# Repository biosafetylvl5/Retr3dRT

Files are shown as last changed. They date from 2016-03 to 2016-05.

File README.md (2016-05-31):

# Retr3dRT
RAMPS 1.4 self-test board designed for used in conjunction with Retr3d.

## Images
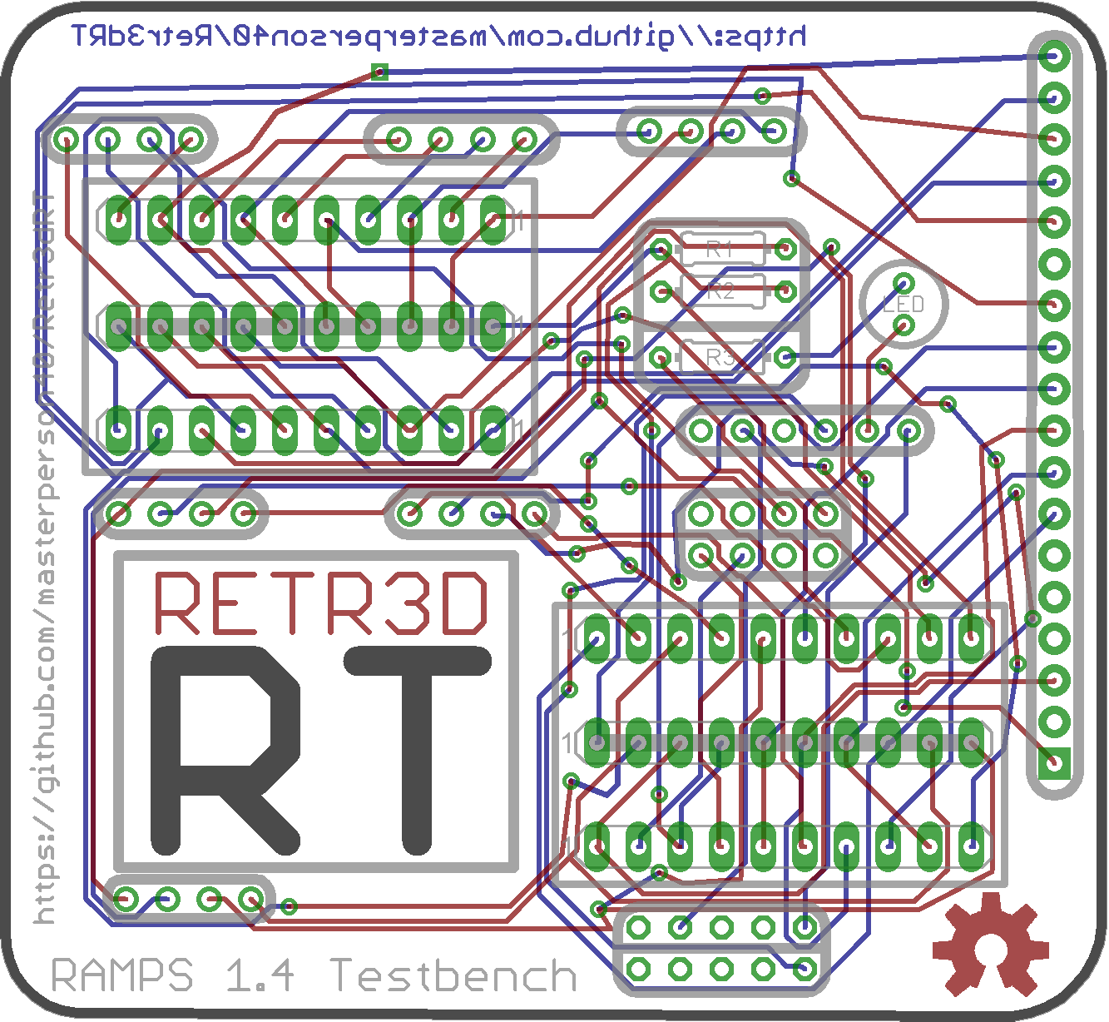
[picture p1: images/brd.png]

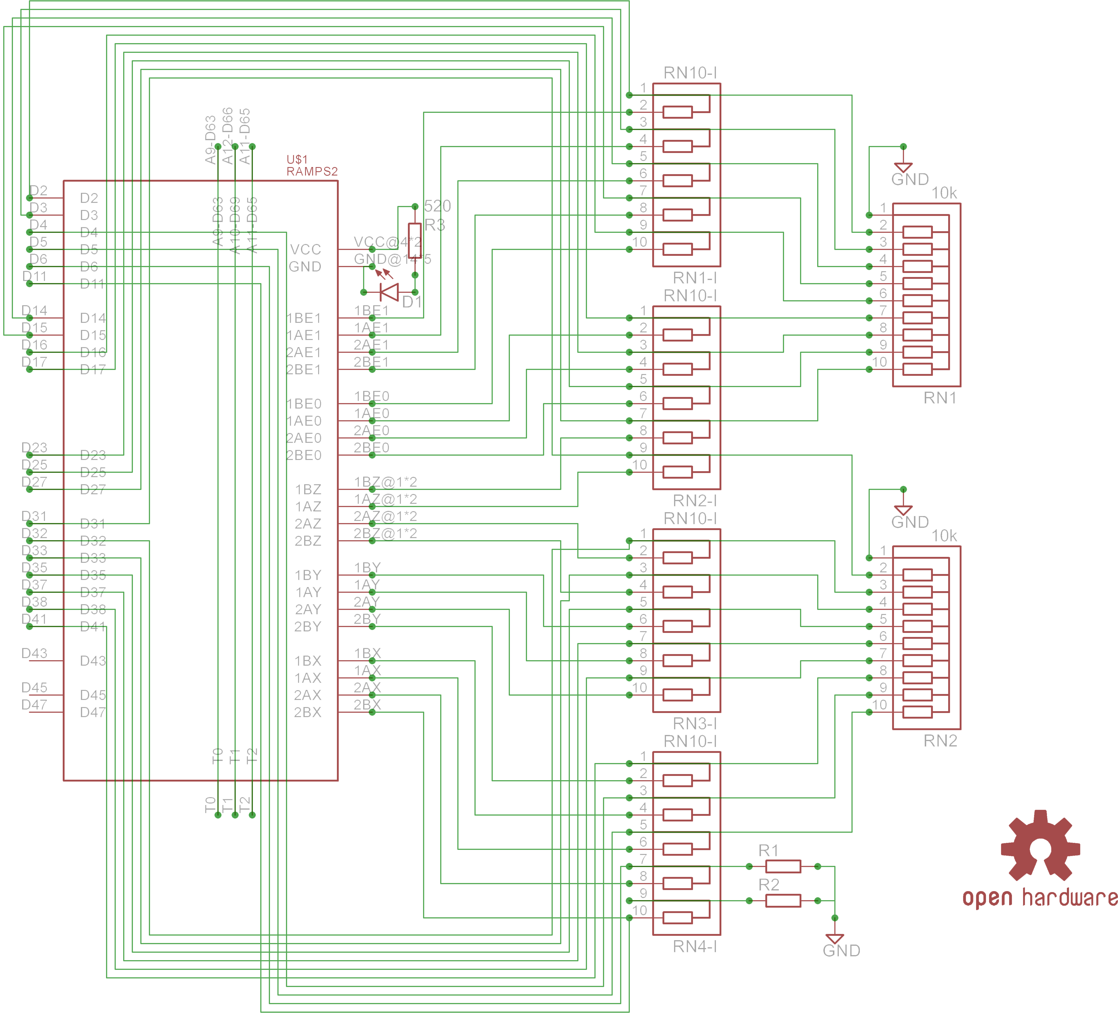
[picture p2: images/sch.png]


#### OSHPark Renderings
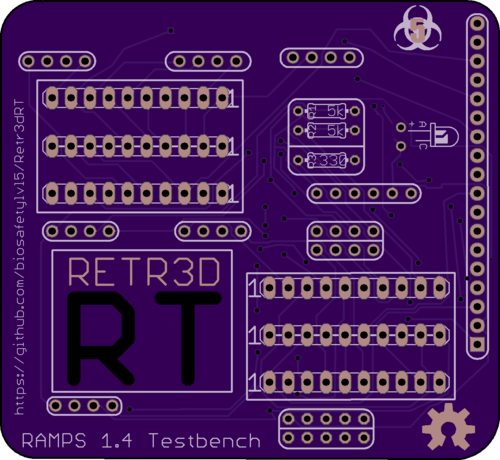
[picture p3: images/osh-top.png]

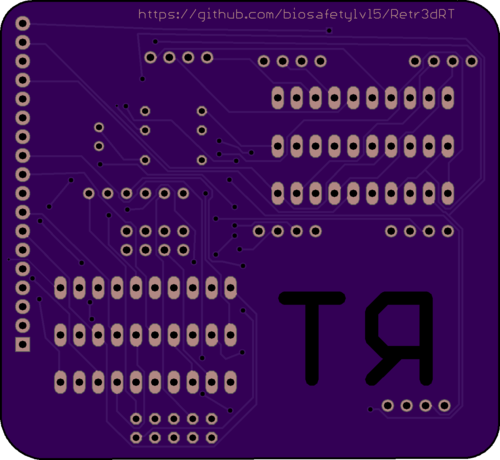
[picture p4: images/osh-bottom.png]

# Make Retr3dRT

## Parts

Check your parts! The easiest way to make an functional Retr3dRT and not know why it's not working to use the wrong parts.

Part            | Picture                                                                                                   | Description                                                | Quantity |                                                                              Distributer
--------------- | --------------------------------------------------------------------------------------------------------- | ---------------------------------------------------------- | :------: | ---------------------------------------------------------------------------------------:
Retr3dRT        | Board             | Circuit board, see "PCB Fabrication" for more info         |    1     |                                                                    OSH Park, SeeedStudio
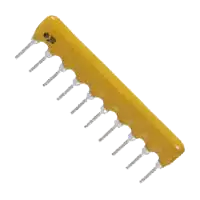
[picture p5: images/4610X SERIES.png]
4601X SERIES
4610X-101-502LF |  | Nine 5K Ohm Resistor Array, 10SIP                          |    2     |                                           [DigiKey](http://www.digikey.com/short/3p0zrv)
4610X-101-153LF | 4601X SERIES | Five 15k Ohm Resistor Array, 10SIP                         |    4     |                                           [DigiKey](http://www.digikey.com/short/3p0zw4)
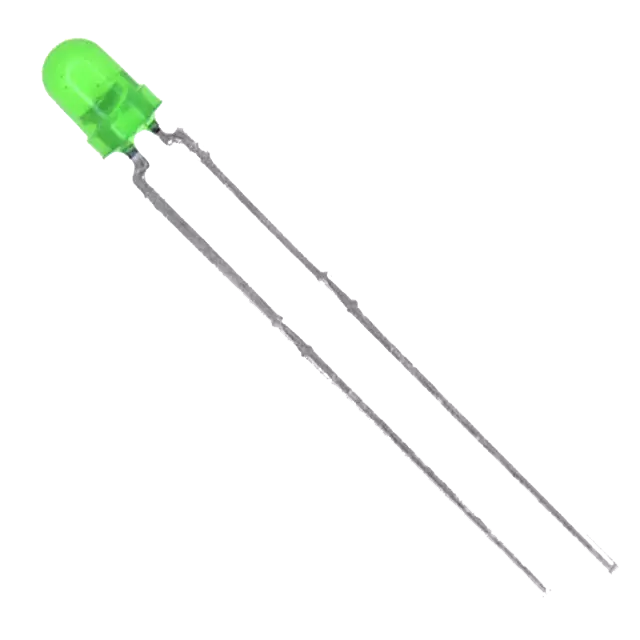
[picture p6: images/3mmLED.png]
3MM LED
LED-3MM         |             | 3mm LED (Preferably Green)                                 |    1     |                                    [DigiKey](http://www.digikey.com/short/3p0z0f), Other
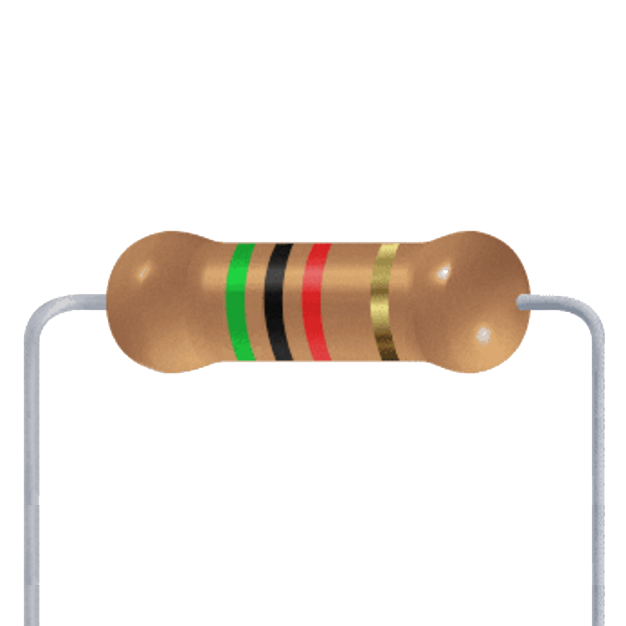
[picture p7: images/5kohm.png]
R1, R2          |         | 5k Ohm Resistor                                            |    2     |                                    [DigiKey](http://www.digikey.com/short/3p0z1c), Other
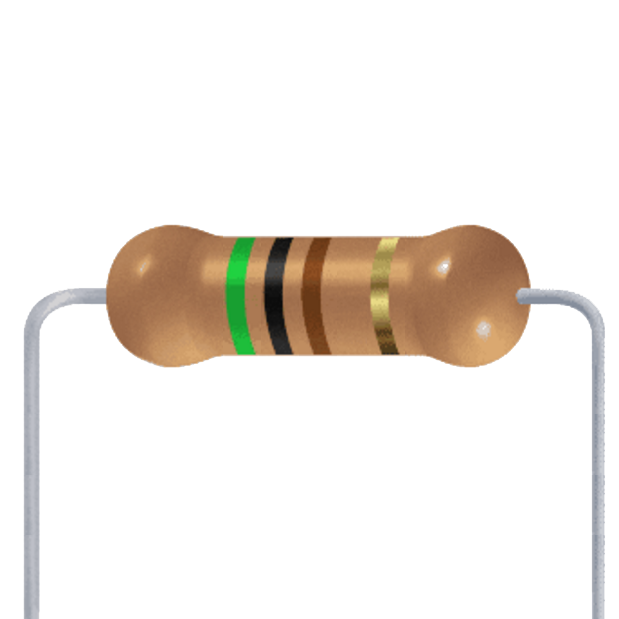
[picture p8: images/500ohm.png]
R3              |        | LED Current Limiting Resistor (520 Ohm is a safe estimate) |    1     |                                    [DigiKey](http://www.digikey.com/short/3p0z1r), Other
3461260P1       | 4601X SERIES      | DIP Long Blue Female Header                                |    7     | [Pending](http://www.seeedstudio.com/wiki/File:1X6P-2.54-8.5%2B2.5-12.3-BLUE-FEMALE.zip)

## Soldering

Now that you have your parts, let's get assembling! If you are just getting started in Electronics, check out [Lady Ada's Guide to Excellent Soldering](https://learn.adafruit.com/adafruit-guide-excellent-soldering/) to brush up on your soldering skills.

Start by soldering R1, R2, and R3 into place. Follow by soldering the LED paying special attention to the polarity annotated on the board. Next, solder the 4610X-101-153LFs and 4610X-101-502LFs by placing them in their holes and securing them with sticky tape. The stick tape prevents them from falling out as you turn the board upside down to solder.

Now, you should have all of the components except for the header soldered. To start the headers, get your diagonal cutters out. Use the diagonal cutters to cut the twelve long headers into eight four long headers, two five long header, one six long header, one eight long header and one complete twelve long header. Now that all of your headers have been prepared, plug them into your RAMPS control board that has its **stepper drivers installed**. Now, carefully lower your Retr3dRT onto the pins and solder it in place.

## Using

Download [Retr3dRT.ino](https://raw.githubusercontent.com/biosafetylvl5/Retr3dRT/master/Retr3dRT.ino) from the [Retr3dRT repository](https://github.com/biosafetylvl5/Retr3dRT) and upload it to your Arduino MEGA with both RAMPS and Retr3dRT installed on top. To view the diagnosis, open your serial terminal and bask in the glow of the information.

## Keeping in touch

To keep in touch to watch for updates and improvements you have a few options:

- [Star the Retr3dRT repository](https://github.com/biosafetylvl5/Retr3dRT/stargazers) to be kept up to date
- Follow the [#Retr3dRT hashtag](https://twitter.com/hashtag/Retr3dRT?f=tweets&src=hash) on twitter to know the moment things happen
- Check out [techfortrade](techfortrade.org) to see what else we're doing

## PCB Fabrication
We're lucky enough to live in the era of cheap and abundant PCB fabrication options. However, this abundance of choices does make choosing a formidable task. However, too make the choosing easier for you, we've narrowed down
the choices to two for you. You're free to choose any fabrication vendor, but we will only be offering (unless asked for others) gerber files (PCB blueprints) for SeeedStudio and OSHPark.

### OSHPark
OSHPark is fantastic. Their boards look great and arrive quickly. However, at 5$ per square inch for three boards, they can be costly for larger runs. Other than that, they have produced good results. This is probably the choice for you if you need
three boards or less.

### SeeedStudio
While SeeedStudio is the budget choice, this isn't a statement about their quality. They feature vanilla PCBs that are very functional, but aren't the most aesthetically pleasing. They deliver quickly, but slower than OSHPark (in the USA) given that they're based in china. This is probably the choice for you if you need more than three boards.

### Final Notes

This board assumes that PCB traces are not faulty. Although this is a possibility, the board was not designed explicitly to test poor traces, it is highly probable that the results from tests meant to test intra-board connections will also flag trace problems.

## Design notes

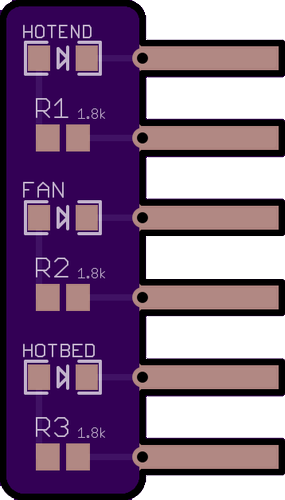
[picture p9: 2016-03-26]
images/osh-top2.png

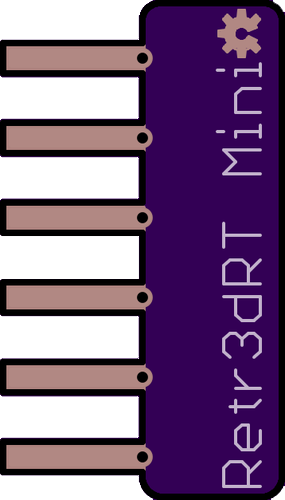
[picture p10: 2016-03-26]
images/osh-bottom2.png

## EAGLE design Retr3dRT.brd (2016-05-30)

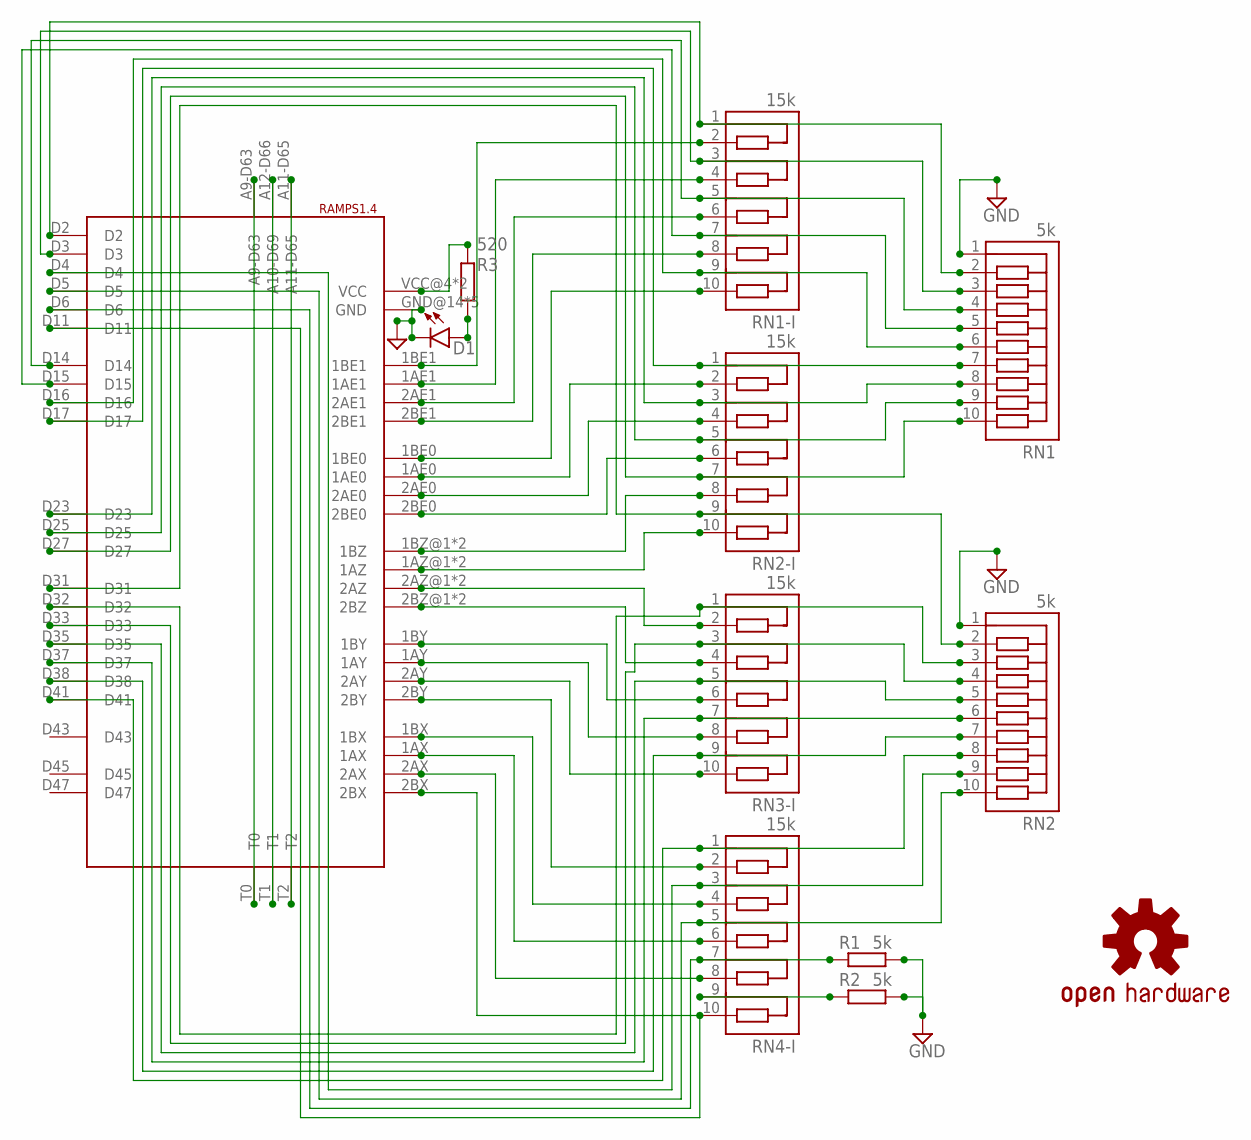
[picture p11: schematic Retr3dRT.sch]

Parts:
D1: LED; LED3MM-NS
LOGO2: OSHW-LOGOL-COPPER; OSHW-LOGO-L_COPPER
R1, R2: 5k; 0204/7
R3: 520; 0204/7
RAMPS1.4: RAMPS2
RN1, RN2: 5k; RN10
RN1-I, RN2-I, RN3-I, RN4-I: 15k; RN10

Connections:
GND: D1.K (C), R1.2, R2.2, RAMPS1.4.GND@14 (GND), RAMPS1.4.GND@16 (GND), RAMPS1.4.GND@17 (GND), RAMPS1.4.GND@18 (GND), RAMPS1.4.GND@19 (GND), RN1.1, RN2.1
unnamed: RAMPS1.4.D23, RN1.8, RN2-I.3
unnamed: RAMPS1.4.2AZ@1 (2AZ), RAMPS1.4.2AZ@2 (2AZ), RN3-I.2
unnamed: RAMPS1.4.1BY, RN3-I.6
unnamed: RAMPS1.4.2AY, RN3-I.10
unnamed: RAMPS1.4.2BY, RN4-I.2
unnamed: RAMPS1.4.1BX, RN4-I.4
unnamed: RAMPS1.4.1AX, RN4-I.6
unnamed: RAMPS1.4.1AY, RN3-I.8
unnamed: R1.1, RAMPS1.4.D6, RN4-I.7
unnamed: RAMPS1.4.2BZ@1 (2BZ), RAMPS1.4.2BZ@2 (2BZ), RN3-I.4
unnamed: D1.A, R3.2
unnamed: RAMPS1.4.2BX, RAMPS1.4.D11, RN4-I.10
unnamed: R2.1, RN4-I.9
unnamed: RAMPS1.4.A11-D65, RAMPS1.4.T2
unnamed: RAMPS1.4.A12-D66 (A10-D69), RAMPS1.4.T1
unnamed: RAMPS1.4.A9-D63, RAMPS1.4.T0
unnamed: RAMPS1.4.D17, RN1.7, RN2-I.1
unnamed: RAMPS1.4.D16, RN1.6, RN1-I.9
unnamed: RAMPS1.4.D25, RN1.9, RN2-I.5
unnamed: RAMPS1.4.D31, RN2.2, RN2-I.9
unnamed: RAMPS1.4.1BE1, RN1-I.2
unnamed: RAMPS1.4.1AE1, RN1-I.4
unnamed: RAMPS1.4.2AE1, RN1-I.6
unnamed: RAMPS1.4.2BE1, RN1-I.8
unnamed: RAMPS1.4.1BE0, RN1-I.10
unnamed: RAMPS1.4.1AE0, RN2-I.2
unnamed: RAMPS1.4.2AE0, RN2-I.4
unnamed: RAMPS1.4.2BE0, RN2-I.6
unnamed: RAMPS1.4.1BZ@1 (1BZ), RAMPS1.4.1BZ@2 (1BZ), RN2-I.8
unnamed: RAMPS1.4.1AZ@1 (1AZ), RAMPS1.4.1AZ@2 (1AZ), RN2-I.10
unnamed: RAMPS1.4.2AX, RN4-I.8
unnamed: RAMPS1.4.D2, RN1.2, RN1-I.1
unnamed: RAMPS1.4.D3, RN1.3, RN1-I.3
unnamed: RAMPS1.4.D14, RN1.4, RN1-I.5
unnamed: RAMPS1.4.D15, RN1.5, RN1-I.7
unnamed: RAMPS1.4.D27, RN1.10, RN2-I.7
unnamed: RAMPS1.4.D32, RN2.3, RN3-I.1
unnamed: RAMPS1.4.D33, RN2.4, RN3-I.3
unnamed: RAMPS1.4.D35, RN2.5, RN3-I.5
unnamed: RAMPS1.4.D37, RN2.6, RN3-I.7
unnamed: RAMPS1.4.D38, RN2.7, RN3-I.9
unnamed: RAMPS1.4.D41, RN2.8, RN4-I.1
unnamed: RAMPS1.4.D4, RN2.9, RN4-I.3
unnamed: RAMPS1.4.D5, RN2.10, RN4-I.5
VCC: R3.1, RAMPS1.4.VCC@4 (VCC), RAMPS1.4.VCC@6 (VCC)

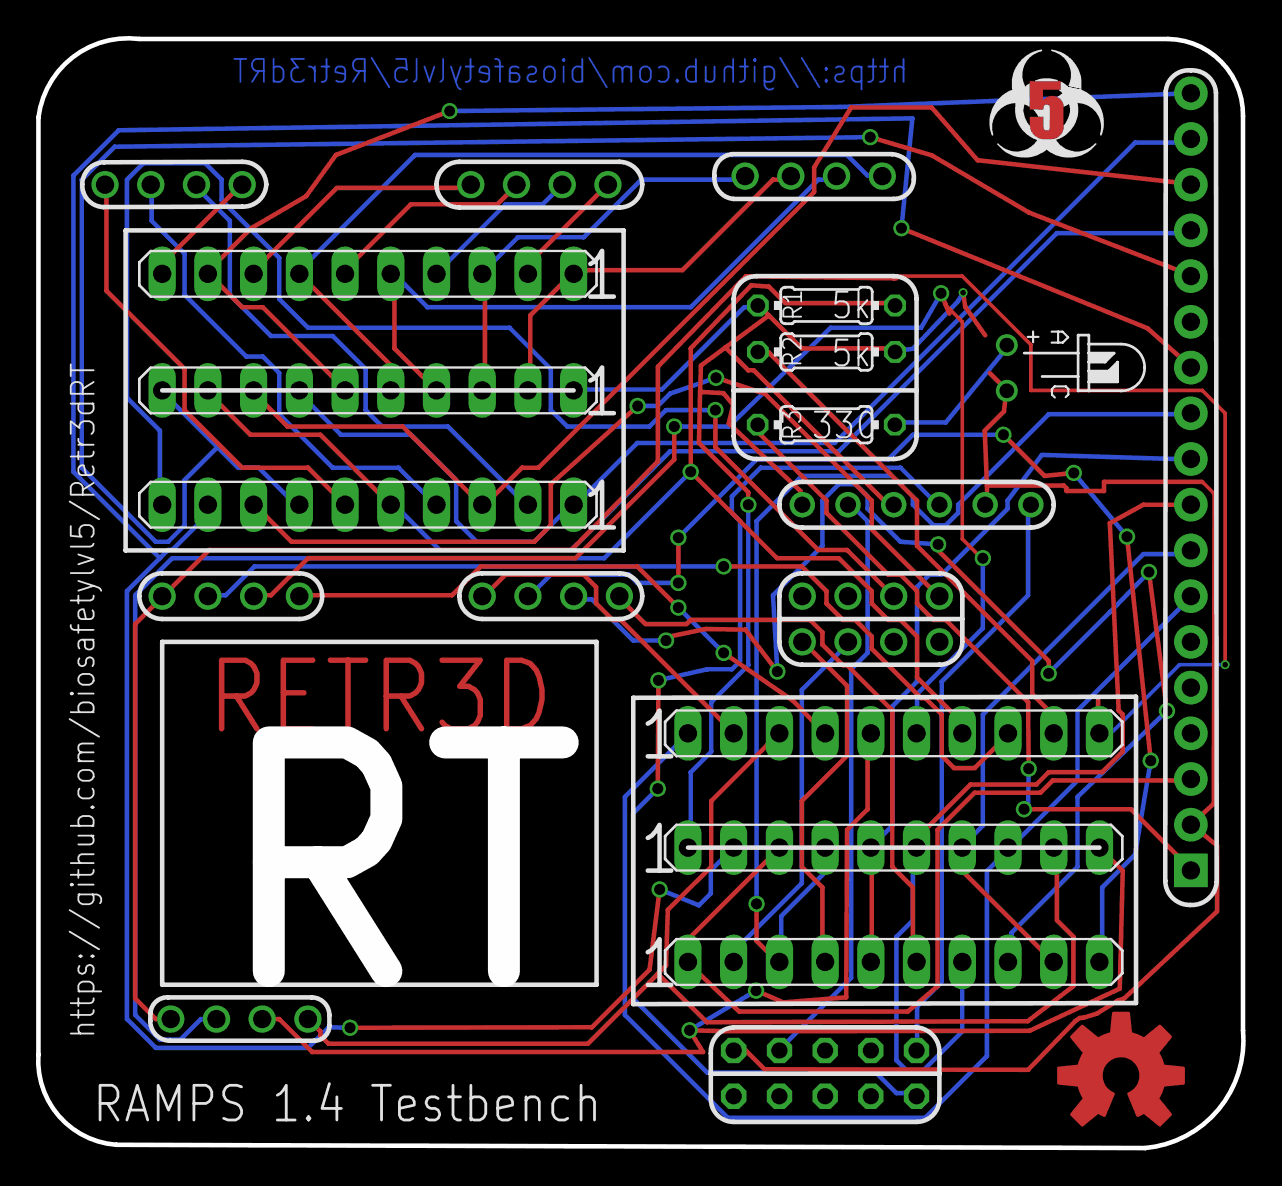
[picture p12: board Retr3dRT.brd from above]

Board: 4 copper layers, 67.0 x 61.7 mm, 14 parts (0 on the bottom side), 46 nets.

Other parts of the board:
E$1: BSL-5-SLK-SML
U$2: LED-GUIDE

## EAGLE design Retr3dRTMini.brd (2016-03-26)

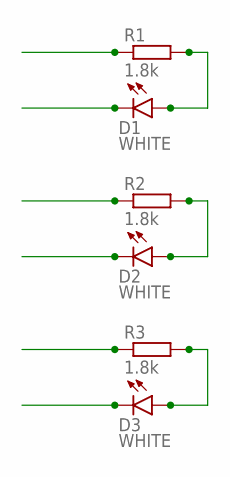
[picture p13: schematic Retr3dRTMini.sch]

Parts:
D1, D2, D3: WHITE; LED-1206
R1, R2, R3: 1.8k; R0805

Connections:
unnamed: D1.A, R1.2
unnamed: D2.A, R2.2
unnamed: D3.A, R3.2
S1: D1.C
S2: R1.1
S3: D2.C
S4: R2.1
S5: D3.C
S6: R3.1

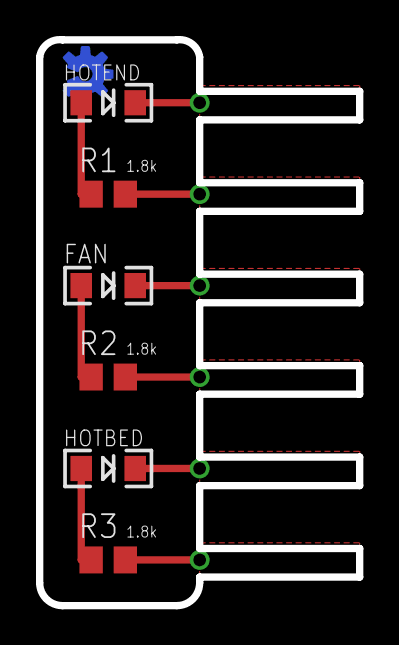
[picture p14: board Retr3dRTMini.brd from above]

Board: 2 copper layers, 17.8 x 31.4 mm, 7 parts (0 on the bottom side), 3 nets.

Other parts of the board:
U$1: OSHW-LOGO-S_COPPER

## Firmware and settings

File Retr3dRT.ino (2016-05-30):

#define X_STEP_PIN         54
#define X_DIR_PIN          55
#define X_ENABLE_PIN       38
#define X_MIN_PIN           3
#define X_MAX_PIN           2

#define Y_STEP_PIN         60
#define Y_DIR_PIN          61
#define Y_ENABLE_PIN       56
#define Y_MIN_PIN          14
#define Y_MAX_PIN          15

#define Z_STEP_PIN         46
#define Z_DIR_PIN          48
#define Z_ENABLE_PIN       62
#define Z_MIN_PIN          18
#define Z_MAX_PIN          19

#define E_STEP_PIN         26
#define E_DIR_PIN          28
#define E_ENABLE_PIN       24

#define Q_STEP_PIN         36
#define Q_DIR_PIN          34
#define Q_ENABLE_PIN       30

#define SDPOWER            -1
#define SDSS               53
#define LED_PIN            13

#define FAN_PIN            9

#define PS_ON_PIN          12
#define KILL_PIN           -1

#define HEATER_0_PIN       10
#define HEATER_1_PIN       8
#define TEMP_0_PIN          13   // ANALOG NUMBERING
#define TEMP_1_PIN          14   // ANALOG NUMBERING

void activateStep(){
  
    digitalWrite(X_STEP_PIN    , HIGH);
    digitalWrite(Y_STEP_PIN    , HIGH);
    digitalWrite(Z_STEP_PIN    , HIGH);
    digitalWrite(E_STEP_PIN    , HIGH);
    digitalWrite(Q_STEP_PIN    , HIGH);     
    delay(5);
    
    digitalWrite(X_STEP_PIN    , LOW);
    digitalWrite(Y_STEP_PIN    , LOW);
    digitalWrite(Z_STEP_PIN    , LOW);
    digitalWrite(E_STEP_PIN    , LOW);
    digitalWrite(Q_STEP_PIN    , LOW);     
    delay(5);
    
    digitalWrite(X_STEP_PIN    , HIGH);
    digitalWrite(Y_STEP_PIN    , HIGH);
    digitalWrite(Z_STEP_PIN    , HIGH);
    digitalWrite(E_STEP_PIN    , HIGH);
    digitalWrite(Q_STEP_PIN    , HIGH);     
    delay(5);
    
    digitalWrite(X_STEP_PIN    , LOW);
    digitalWrite(Y_STEP_PIN    , LOW);
    digitalWrite(Z_STEP_PIN    , LOW);
    digitalWrite(E_STEP_PIN    , LOW);
    digitalWrite(Q_STEP_PIN    , LOW);   
    delay(5);
}

void setup() {
  
  Serial.begin(9600);
  Serial.println("Remember to have 12v supplied to the board when testing");
  Serial.println("Failure to do so will produce faulty results\n");  //2, 3, 4, 5, 6, 11, 14, 15, 16, 17, 23, 25, 27, 31, 32, 33, 35, 37, 38, 41};
  const int pins[] = {//2, 3, 4, 5, 6, 11, 14, 15, 16, 17, 23, 25, 27, 31, 32, 33, 35, 37, 38, 41};
                      16, 17, 23, 25,
                      2,  3,  14, 15,
                      4,  5,  6,  11,
                      35, 37, 38, 41,
                      27, 31, 32, 33
                      };

  char* names[]={"E0:1", "E0:2", "E0:3", "E0:4",
                     "E1:1", "E1:2", "E1:3", "E1:4",
                     "X:1 ",  "X:2 ",  "X:3 ",  "X:4 ",
                     "Y:1 ",  "Y:2 ",  "Y:3 ",  "Y:4 ",
                     "Z:1 ",  "Z:2 ",  "Z:3 ",  "Z:4 ",
                     };

  int oldValues[19];
  int newValues[19];
  int i=0;
  
  pinMode(32 , INPUT);
  
  pinMode(FAN_PIN , OUTPUT);
  pinMode(HEATER_0_PIN , OUTPUT);
  pinMode(HEATER_1_PIN , OUTPUT);
  pinMode(LED_PIN  , OUTPUT);
  
  pinMode(X_STEP_PIN  , OUTPUT);
  pinMode(X_DIR_PIN    , OUTPUT);
  pinMode(X_ENABLE_PIN    , OUTPUT);
  
  pinMode(Y_STEP_PIN  , OUTPUT);
  pinMode(Y_DIR_PIN    , OUTPUT);
  pinMode(Y_ENABLE_PIN    , OUTPUT);
  
  pinMode(Z_STEP_PIN  , OUTPUT);
  pinMode(Z_DIR_PIN    , OUTPUT);
  pinMode(Z_ENABLE_PIN    , OUTPUT);
  
  pinMode(E_STEP_PIN  , OUTPUT);
  pinMode(E_DIR_PIN    , OUTPUT);
  pinMode(E_ENABLE_PIN    , OUTPUT);
  
  pinMode(Q_STEP_PIN  , OUTPUT);
  pinMode(Q_DIR_PIN    , OUTPUT);
  pinMode(Q_ENABLE_PIN    , OUTPUT);
  
  digitalWrite(X_ENABLE_PIN    , LOW);
  digitalWrite(Y_ENABLE_PIN    , LOW);
  digitalWrite(Z_ENABLE_PIN    , LOW);
  digitalWrite(E_ENABLE_PIN    , LOW);
  digitalWrite(Q_ENABLE_PIN    , LOW);
  digitalWrite(X_DIR_PIN    , LOW);
  digitalWrite(Y_DIR_PIN    , LOW);
  digitalWrite(Z_DIR_PIN    , LOW);
  digitalWrite(E_DIR_PIN    , LOW);
  digitalWrite(Q_DIR_PIN    , LOW);

  activateStep();
  
  i=0;
  for (i = 0; i < 20; i = i + 1) { oldValues[i]=digitalRead(pins[i]); }
  
  activateStep();
  
  i=0;
  for (i = 0; i < 20; i = i + 1) { newValues[i]=digitalRead(pins[i]); }
  
  i=0;
  for (i = 0; i < 20; i = i + 1) {
    if(!(oldValues[i]==newValues[i])){
      Serial.print(names[i]);
      Serial.println(" Working");
    }else{
      Serial.print(names[i]);
      Serial.println(" Faulty");
      }
  }
  
  analogWrite(A13, 0);
  analogWrite(A14, 0);
  analogWrite(A15, 0);
  int zero = analogRead(A9);
  int one = analogRead(A10);
  int two = analogRead(A11);
  if(zero<700){ Serial.println("T0:  Working"); }else{Serial.println("T0:  Faulty"); }
  if(one<700){  Serial.println("T1:  Working"); }else{Serial.println("T1:  Faulty"); }
  if(two<700){  Serial.println("T2:  Working"); }else{Serial.println("T2:  Faulty"); }
}





void loop () {
  
  if (millis() %1000 <500) 
    digitalWrite(LED_PIN, HIGH);
  else
   digitalWrite(LED_PIN, LOW);
  
  if (millis() %1000 <300) {
    digitalWrite(HEATER_0_PIN, HIGH);
    digitalWrite(HEATER_1_PIN, LOW);
    digitalWrite(FAN_PIN, LOW);
  } else if (millis() %1000 <600) {
    digitalWrite(HEATER_0_PIN, LOW);
    digitalWrite(HEATER_1_PIN, HIGH);
    digitalWrite(FAN_PIN, LOW);
  } else  {
    digitalWrite(HEATER_0_PIN, LOW);
    digitalWrite(HEATER_1_PIN, LOW);
    digitalWrite(FAN_PIN, HIGH);
  }
   activateStep();
  delay(50);
}

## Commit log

2016-03-08 Inital Commit
    [SHIELD.brd, SHIELD.sch]
2016-03-15 Added images
    [SHIELD.brd]
2016-03-15 Updated Design
    [SHIELD.brd]
2016-03-26 Schematic Changes
    [SHIELD.sch]
2016-03-26 Added Retr3dRTMini
    [Retr3dRTMini.brd, Retr3dRTMini.sch]
2016-03-31 Added Gerbers
2016-05-30 Fixed disconnect between grounds
    [Retr3dRT.brd, Retr3dRT.sch]
2016-05-30 Added OSHPark Gerbers
    [SHIELD.brd, SHIELD.sch]
2016-05-30 Added Arduino Sketch
2016-05-30 Fixed silkscreen of R1 and R2
    [Retr3dRT.brd]
2016-05-30 Added Seeed Gerbers
2016-05-30 Updated Board Images
2016-05-31 Added PCB Fab Section

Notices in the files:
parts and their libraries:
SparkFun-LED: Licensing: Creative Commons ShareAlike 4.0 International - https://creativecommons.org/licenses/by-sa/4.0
